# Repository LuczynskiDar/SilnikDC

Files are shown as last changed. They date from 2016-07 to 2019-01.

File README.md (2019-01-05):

# DC Engine driver ( Sterownik prędkości silnika DC )

> DC Engine driver is a [post graduate thesis](https://github.com/LuczynskiDar/SilnikDC/blob/master/Praca%20Podyplomowa%20-%20Sterownik%20Silnika%20-%20Dariusz%20%C5%81uczy%C5%84ski.pdf) done for AGH Univerisity of Science and Technology.

## Purpose of project

The purose of project was to use ECAD, EAGLE to design a circuit analog with
PCBA, then wirte a C program for Atmega32 to dirive a DC Enginge.

### Design approach

- For the project purposes will be used an mocro's internal clock,instead of using more reliable external crystal.
- Drivig the engine will be done on the basis of 4 switches, 2 for changing engine directions (Left/Right),
  which is actually changing micro's GPIO  and 2 responsible for incrementing and decrementing PWM signal.
- Interruption mechanism won't be used.
- I will use built in Fast PWM mechanism.
- The software will be done in C, usng Atmega Studio 7.
- The code will be debugged and uploaded thoreugh JTAG with MK7 Dragn programmer.
- Thce code will be validated with an eval board, Kamami ZL3.

### Block diagram

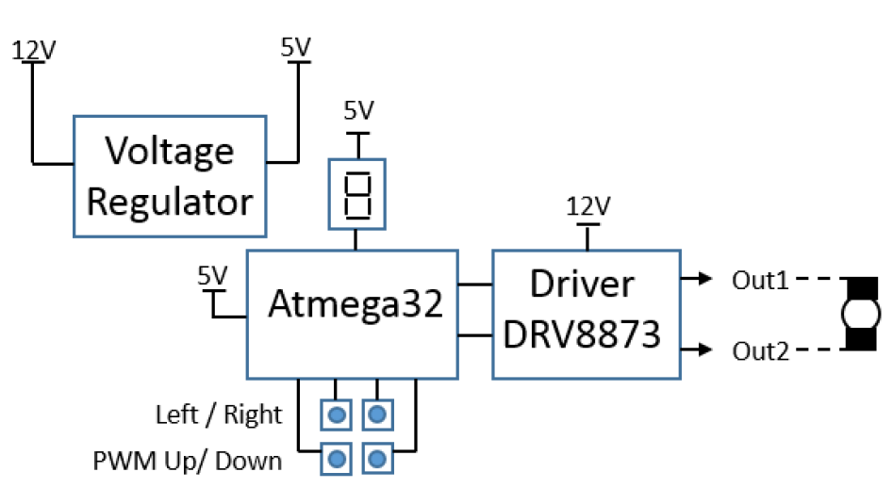
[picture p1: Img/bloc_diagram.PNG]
Block diagram


### Eagle ECAD designer

There are 2 Eagle project files:

- [Sterownik_DC.sch](https://github.com/LuczynskiDar/SilnikDC/blob/master/Sterownik_DC.sch) 
- [Sterownik_DC.brd](https://github.com/LuczynskiDar/SilnikDC/blob/master/Sterownik_DC.brd)

#### Schematic drawing

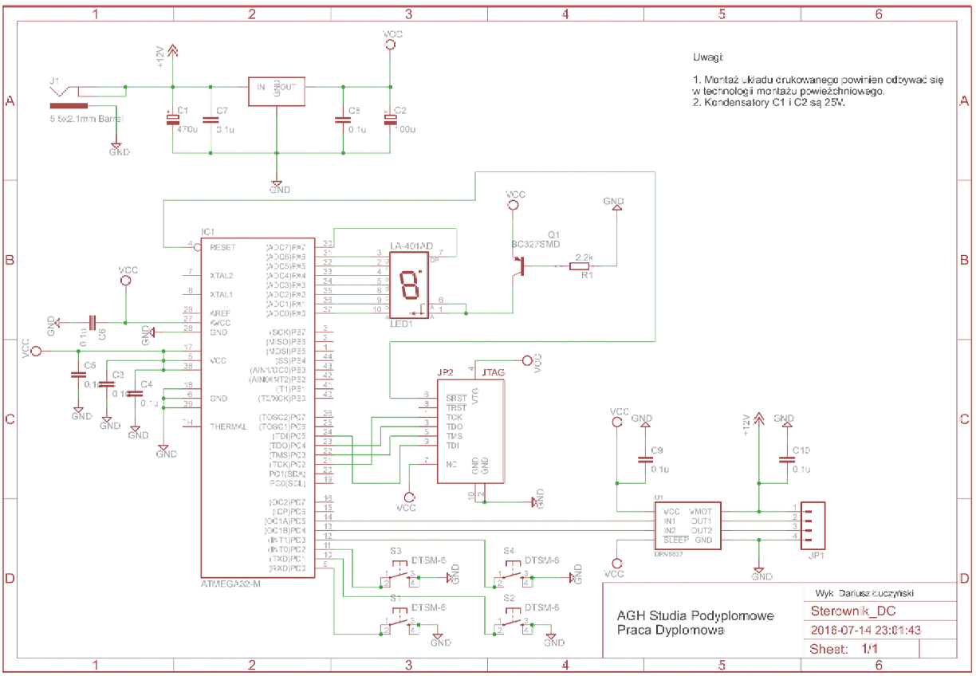
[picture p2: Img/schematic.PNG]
Schematics


#### Material List (BOM)

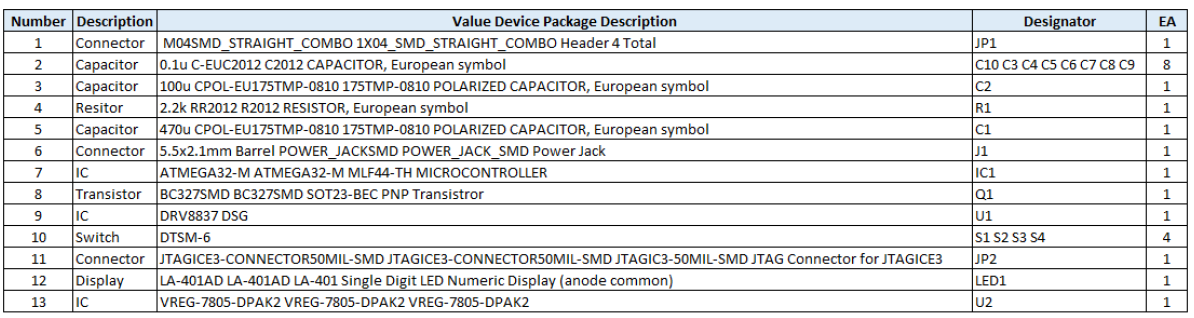
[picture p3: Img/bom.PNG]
BOM


#### Printed wiring board

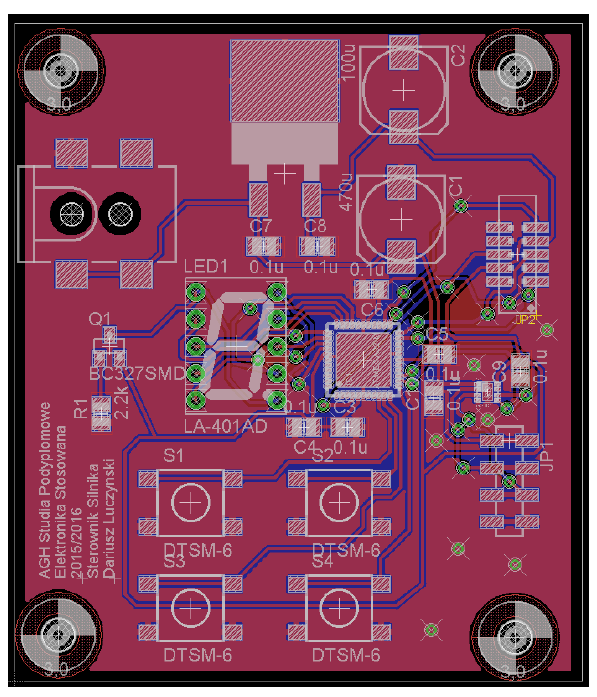
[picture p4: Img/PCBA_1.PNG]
PCBA view


#### PWB Drawing

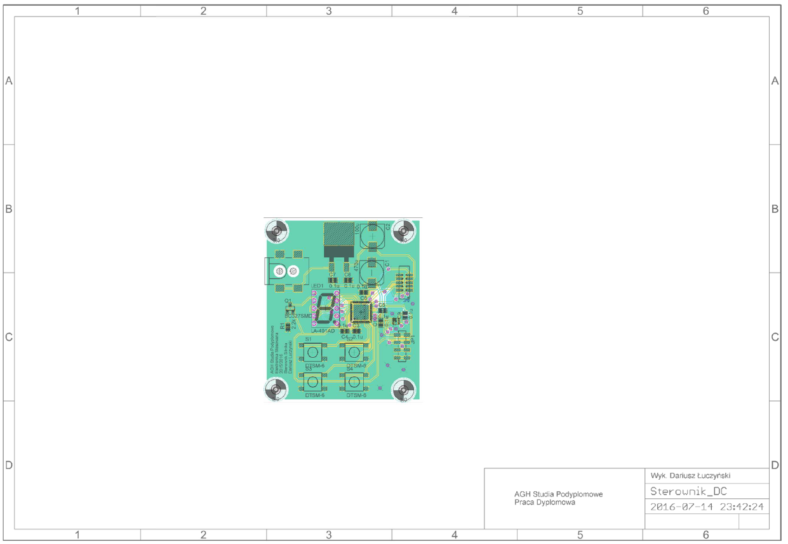
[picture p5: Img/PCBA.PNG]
PCBA drawing view


### C Code

I created 2 files,

- [constants.h](https://github.com/LuczynskiDar/SilnikDC/blob/master/Sterownik_DC/constants.h), which contains definition for an internal clock flags,
- [sterownikdc.c](https://github.com/LuczynskiDar/SilnikDC/blob/master/Sterownik_DC/sterownikdc.c), which contains other methods along with main loop ```while(1)```.

### Design Verification

Code verificationn was performed on eval board, all 4 swithches were working properly.

- Set the dc engine to turn left, "l" on the display.

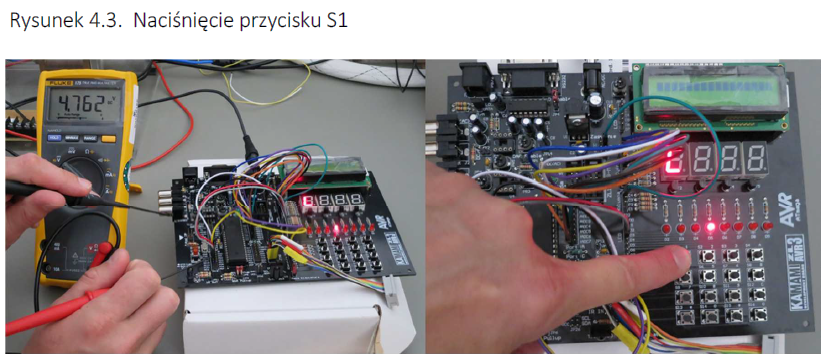
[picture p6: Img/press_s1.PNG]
Press S1


- Set the dc engine to turn right, "r" on te display.

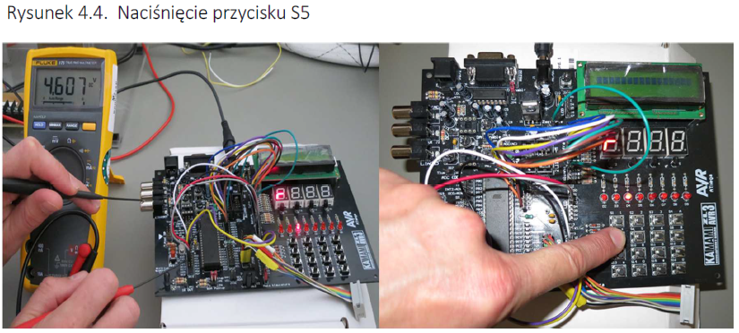
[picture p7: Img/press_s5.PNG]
Press S5


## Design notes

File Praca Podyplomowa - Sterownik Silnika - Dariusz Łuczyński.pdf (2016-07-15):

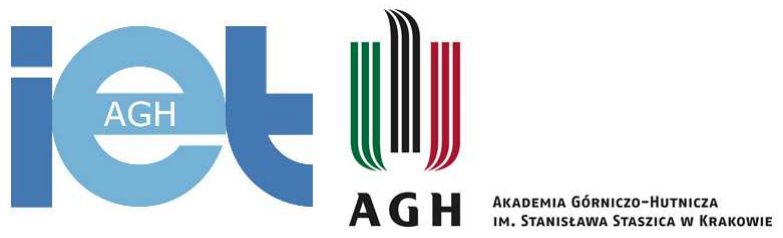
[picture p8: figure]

Studia podyplomowe – Elektronika Stosowana Wydział IEiT, rok akademicki 2015/2016

## Praca Podyplomowa

## Projekt sterownika prędkości silnika DC z wykorzystaniem funkcji PWM mikrokontrolera ATMEGA 32

## Dariusz Łuczyński

2

# Spis Treści

3

# Rozdział 1. Wstęp

Zadaniem poniższej pracy podyplomowej jest projekt urządzenia, które pośredniczy pomiędzy silnikiem prądu stałego a człowiekiem oraz pozwala na jego sterowanie poprzez przyciski. Założeniem przy budowie poniższego sterownika jest spełnianie dwóch funkcji:

- zmiana kierunku obrotów silnika CW/CCW (Clockwise / Counter clockwise);
- zmiana wypełnienia sygnału PWM;

Zmiana kierunku obrotów silnika polega na naprzemiennym załączaniu sygnału sterującego na Out1 i Out2 oraz masy, tj. gdy na Out1 jest sygnał PWM to na Out2 jest masa i na zmianę.

Rysunek 1.1. Schemat ideowy układu.

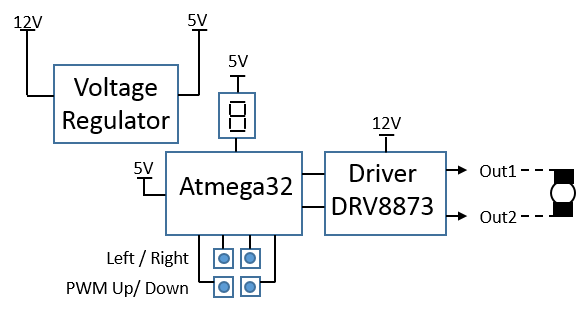
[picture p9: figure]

Rysunek 1.2. Modulacja PWM ( modulacja szerokości impulsu).

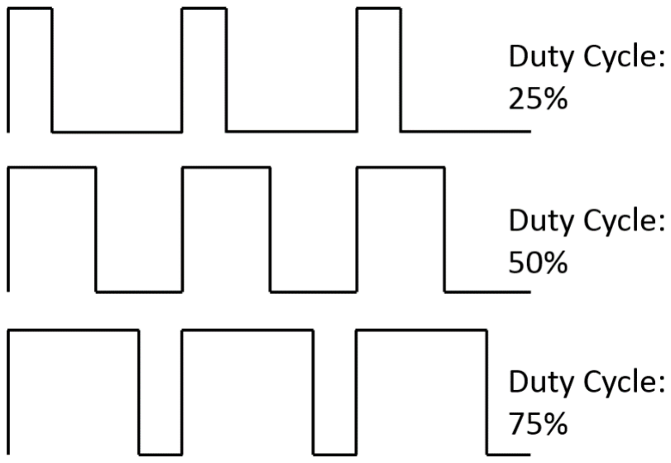
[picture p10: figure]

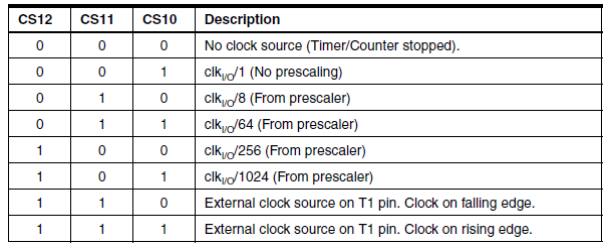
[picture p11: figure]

4

# Rozdział 2. Oprogramowanie mikrokontrolera

Podstawą procesora AVR jest czasomierz/licznik (Timer/Counter), w przypadku Atmega32 są to trzy timery, które zliczają impulsy zegarowe. Po osiągnięciu maksymalnej wartości licznik przekręca się i zaczyna zliczanie od nowa. Częstotliwość sygnału zegarowego określa minimalną rozdzielczość pomiaru, a każde zwiększenie licznika będzie następowało z tą rozdzielczością. Licznik po osiągnięciu wartości maksymalnej zaczyna zliczanie od początku. Atmega32 udostępnia dwa liczniki 8-bit oraz jeden 16-bit. Częstotliwość sygnału zegarowego może być podzielona, zmniejszona poprzez użycie Preskalera, poprzez użycie jednej z predefiniowanych wartości: 1, 8, 64, 256, 1024. Odbywa się to poprzez wybranie odpowiednich bitów Clock Select.

Rysunek 2.1. Preskaler Timera0 oraz Timera1.

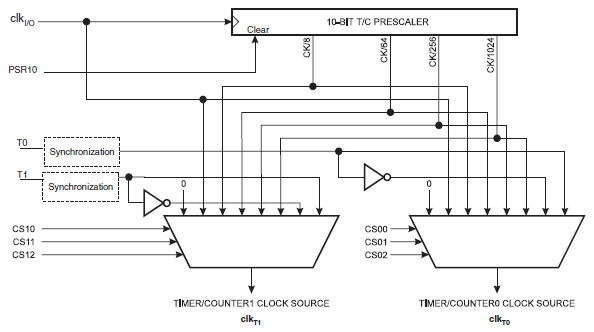
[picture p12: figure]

Tabela 2.1. Ustawienie bitów clock select.

5

Rysunek 2.2. Schemat blokowy Timera1.

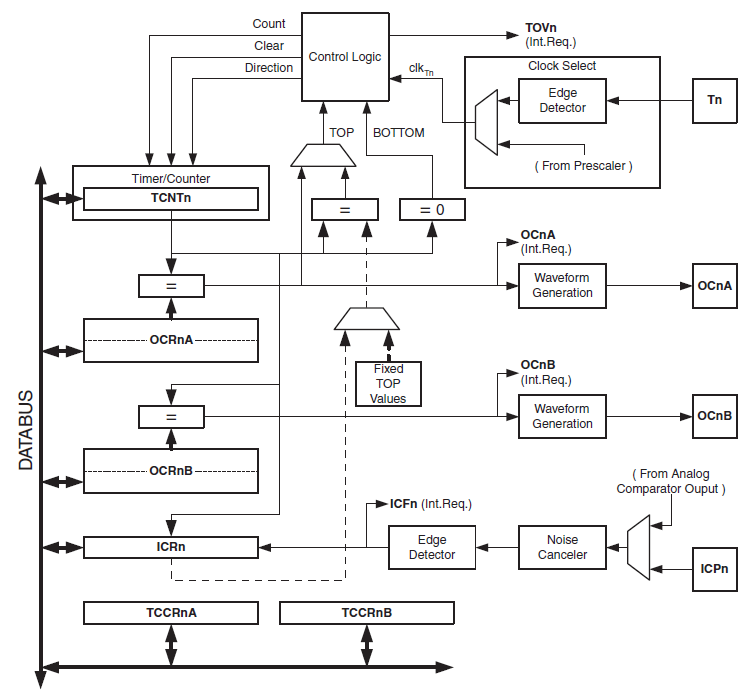
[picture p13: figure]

Początek może być wartością maksymalną, w przypadku liczników 8-bit jest 255, lub wartością minimalną, czyli 0. Mikrokontroler daje możliwość zliczania sygnałów od wartości minimalnej (Bottom) do maksymalnej (Top), oraz w przeciwnym kierunku. Zakładając, że kierunek zliczania impulsów jest w kierunku od Bottom do Top, to po osiągnięciu wartości 255 następuje zmiana flagi przepełnienia licznika TOV1 (Timer Overflow), co może skutkować wykonaniem procedury obsługi przerwania, o ile taka jest zdefiniowana w programie.

Tabela 2.2. Ustawienie bitów Waveform Generation Mode (WGM) dla Timera1

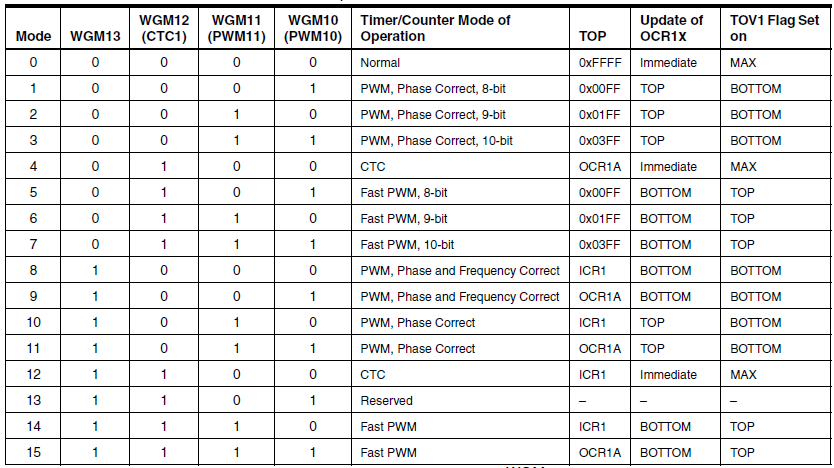
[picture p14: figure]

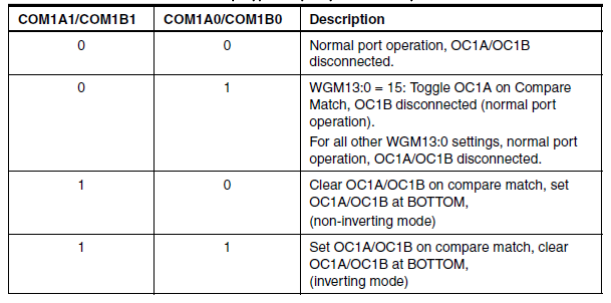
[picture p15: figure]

6

Zliczana wartość przez licznik, rejestr TCNT1, morze zostać porównana z wartością predefiniowaną przez użytkownika, wartością, która znajduje się w rejestrze OCR1A/OCR1B (Output Compare Register). Pozytywny wynik porównania rejestru licznika powoduje ustawienie flagi OCF1A/ OCF1B i skutkuje wystąpieniem zdarzenia Compare Match oraz może powodować wygenerowanie żądania wykonania obsługi przerwania. Compare Match może również służyć do wygenerowania przebiegów na pinach IO procesora, a jego wpływ na PINy jest określany poprzez odpowiednie ustawienie bitów COM0 i COM1.

Tabela 2.3. Znaczenie bitów COM w przypadku pracy timera w trybie FAST PWM

Rysunek 2.3. Tryb Fast PWM.

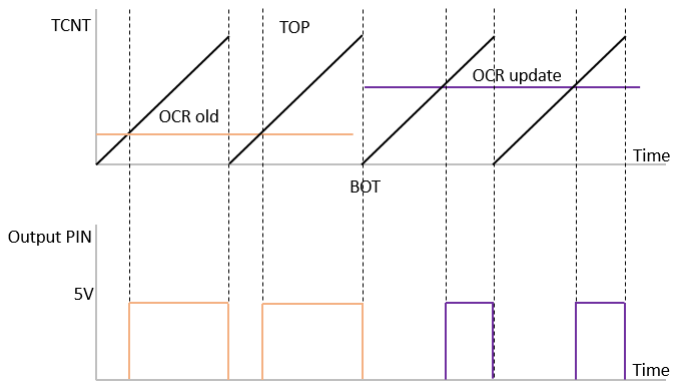
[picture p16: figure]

Stąd oprócz podstawowych funkcjonalności timera, to jest działania, jako licznik oraz precyzyjnego odmierzania czasu, mierzenia czasu między impulsami, dochodzi jeszcze

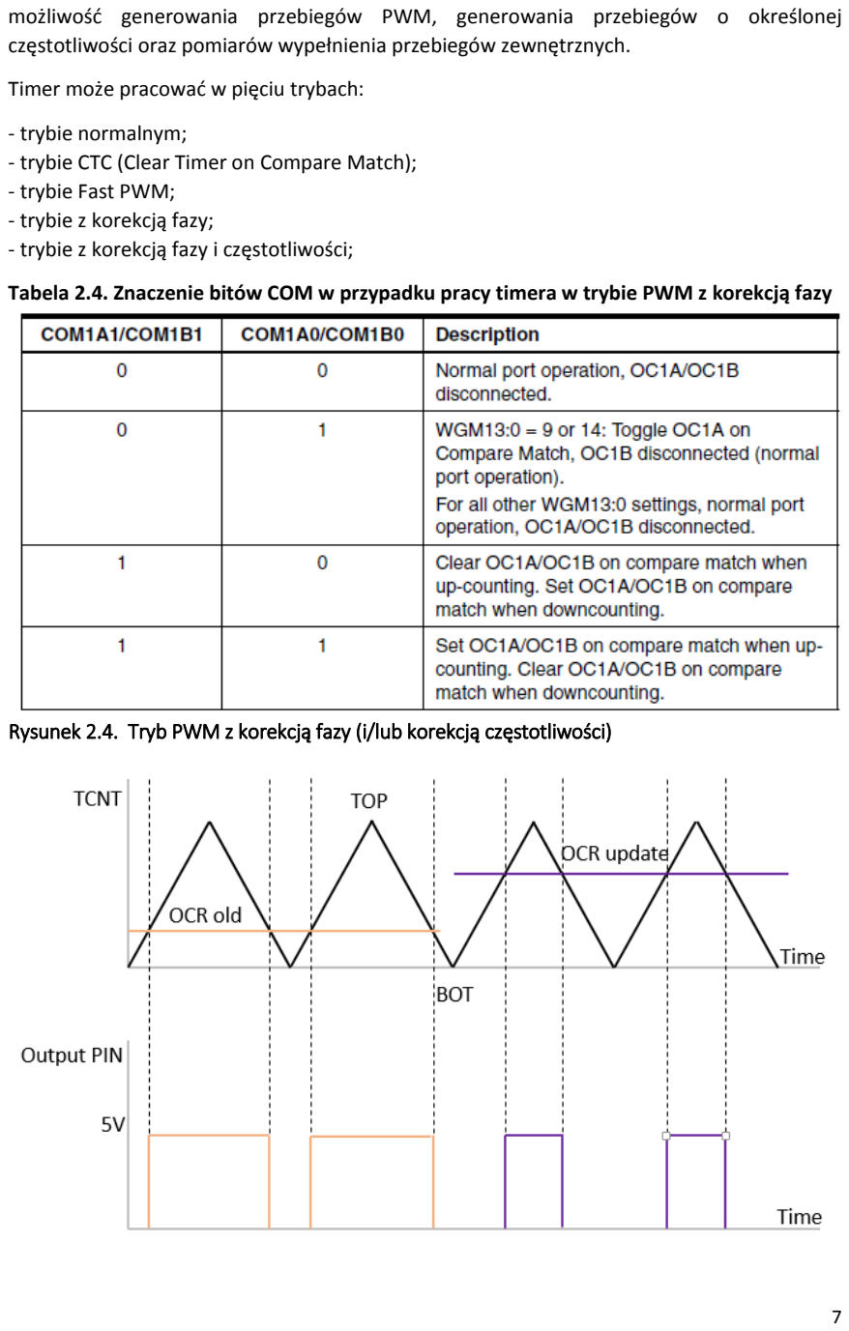
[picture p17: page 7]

7

możliwość generowania przebiegów PWM, generowania przebiegów o określonej częstotliwości oraz pomiarów wypełnienia przebiegów zewnętrznych.

Timer może pracować w pięciu trybach:

- trybie normalnym;
- trybie CTC (Clear Timer on Compare Match);
- trybie Fast PWM;
- trybie z korekcją fazy;
- trybie z korekcją fazy i częstotliwości;

Tabela 2.4. Znaczenie bitów COM w przypadku pracy timera w trybie PWM z korekcją fazy

Rysunek 2.4. Tryb PWM z korekcją fazy (i/lub korekcją częstotliwości)

8

W trybie normalnym, wbudowany Waveform Generation Mode nie jest wykorzystywany, natomiast używa się interwałów czasowych ograniczanych przez preskaler, w których na port wyjściowy, OC0 lub OC1, jest podawany stan wysoki.

Tryb CTC wymaga ustawienia odpowiednich bitów WGM, zgodnie z Tabelą 2.2, w rejestrach TCCR. Umożliwia na precyzyjniejszą kontrolę nad częstotliwością przebiegu na pinach wyjściowych, która wynosi Fclk / (2*Preskaler*(1+OCR1A)). Licznik zlicza do OCR1A, i za każdym razem, gdy osiąga tą wartość, generowane jest zdażenie TIMER1 COMP lub TIMER1 CAPT (o ile ustawiamy ICR). Przerwanie przepełnienia licznika TIMER1 OVF nie występuje, licznik nie zlicza do maksymalnej wartości.

Podobnie jak CTC tryb Fast PWM wymaga odpowiedniego zdefiniowania bitów WGM. Licznik zlicza od wartości Bottom do wartości Top, a po jej osiągnięciu, zlicza ponownie od wartości Bottom. Częstotliwość wynosi Fclk / (*Preskaler*(1+Licznik max)), gdzie Licznik max, jest maksymalną wartością trybu fast PWM, np. dla 8-bit jest to 255.

W przypadku trybów PWM z korekcją fazy oraz z korekcja fazy częstotliwości licznik odlicza od wartości Bottom do Top, a następnie od Top do Bottom, jak na Rysunku 2.4. Częstotliwość wynosi Fclk/(2*Preskaler(1+Wartość Top)). Oba tryby powinny mieć ustawione odpowiednie flagi WGM.

Przed przygotowaniem oprogramowania zostały przyjęte następujące założenia:

- zostanie wykorzystany wewnętrzny zegar mikroprocesora, bez posiłkowania się zewnętrznym rezonatorem kwarcowym;
- sterowanie będzie obywało się za pomocą czterech przycisków, a będzie realizować inkrementację i dekrementację sygnału PWM, a także zmianę wyjścia, na którym jest on podawany;
- do sterowania nie zostanie wykorzystany mechanizm przerwań;
- zostanie wykorzystany tryb Fast PWM;
- oprogramowanie zostanie napisane w języku C;

Oprogramowanie składa się z dwóch plików z kodem źródłowym, „constants.h” zawiera stałe oraz częstotliwość taktu zegarowego, natomiast w „sterownikdc.c” znajduje się pełen kod źródłowy programu.

Główny kod źródłowy programu definiuje globalne flagi, które określają, na jakim PIN jest PWM (OC1 lub OC0), oraz wartość wypełnienia. Jest zdefiniowana również tablica, która zawiera dwie zmienne ośmiobitowe typu unsign integer, służące do wyświetlania na przemian „l” lub „r”, w zależności od kierunku obrotów silnika. Tablica jest umieszczona w pamięci flash. W funkcji Main programu w pierwszej kolejności następuje inicjalizacja Timer1, za pomocą metody timer1_initialize(), ustawienie bitów WGM dla Fast PWM, bitów Compare Match A/B, a także rejestrów Output Compare Register A/B. Kierunek portów A zostaje ustawionyna wyjście, będą one obsługiwać wyświetlacz siedmiosegmentowy. Zostaje zdefiniowana częstotliwość Fclk/ (Preskaler * 256), w tym przypadku 1 MHZ/ ( 8 * 256), 488 Hz. Na czterech mniej znaczących bitach portu D zostaje ustawiony stan wysoki, porty te są wykorzystywane

9

do obsługi przycisków. Nieskończona pętla programu wywołuje kolejno trzy metody. Funkcja scan_key() sprawdza stan przycisków ( jest to tzw. pooling). Odczytywana jest wartość z rejestru PIND, natępenie zmieniana jest flaga lub wartość wypełnienia PWM. w zależności od tego, który przycisk został wciśnięty. Dekrementacja zmiennej counter, służy, jako mikroopóźnienie, ze względu na mechaniczne drgania przycisków występujące po ich naciśnięciu, „bouncing”. Funkcja show_direction() przełącza kierunek obrotów silnika oraz zmienia pokazywaną literę na wyświetlaczu siedmiosegmentowym. Ostatnia w kolejności metoda pwm_set() ma za zadanie ustawienie we właściwym OCR, wartości wypełnienia, która została uprzednio inkrementowana lub dekrementowana.

10

# Rozdział 3. Schemat elektryczny i obwód drukowany

Do układu zostaje doprowadzone 12V DC z zewnętrznego zasilacza impulsowego do 2.1 mm gniazda, które zostaje przekształcone na napięcie 5V, przy użyciu popularnej przetwornicy 7805.

Rysunek 3.1. Schemat stabilizatora napięcia.

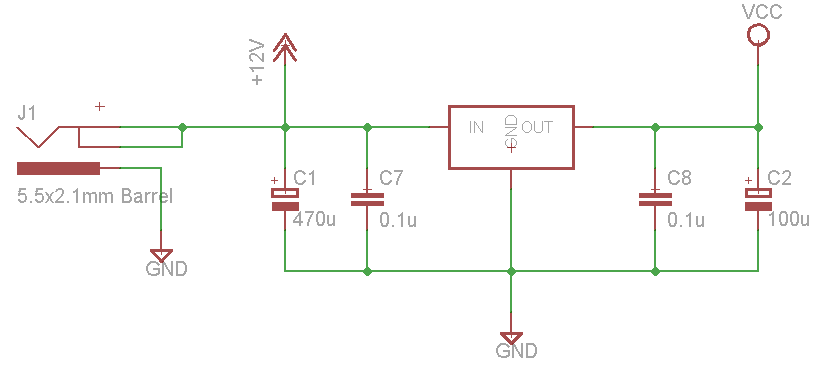
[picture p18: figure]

Z portu A zostało wyprowadzonych osiem bitów kontrolujących wyświetlacz siedmiosegmentowy, w tym DP. Zasilanie jest wpięte poprzez tranzystor BC327. Wyświetlacz jest typu: wspólna anoda. Musi zostać podany stan niski, aby świeciły poszczególne segmenty. Do portu C jest doprowadzony interfejs JTAG. Do portu D0~D3 zostały przyłączone linie odpowiadające za przyciski. Na liniach utrzymuje się stan wysoki, dopóki dany przycisk nie zostanie naciśnięty, zwarty do masy. Linie D4 (OC1B) i D5 (OC1A) doprowadzają sygnał PWM do drivera. W projekcie został użyty driver DRV8837 TI, niemniej nie jest to najlepszy wybór, ponieważ Vmot, 12V, w tym przypadku przekracza maksymalne napięcie z karty katalogowej.

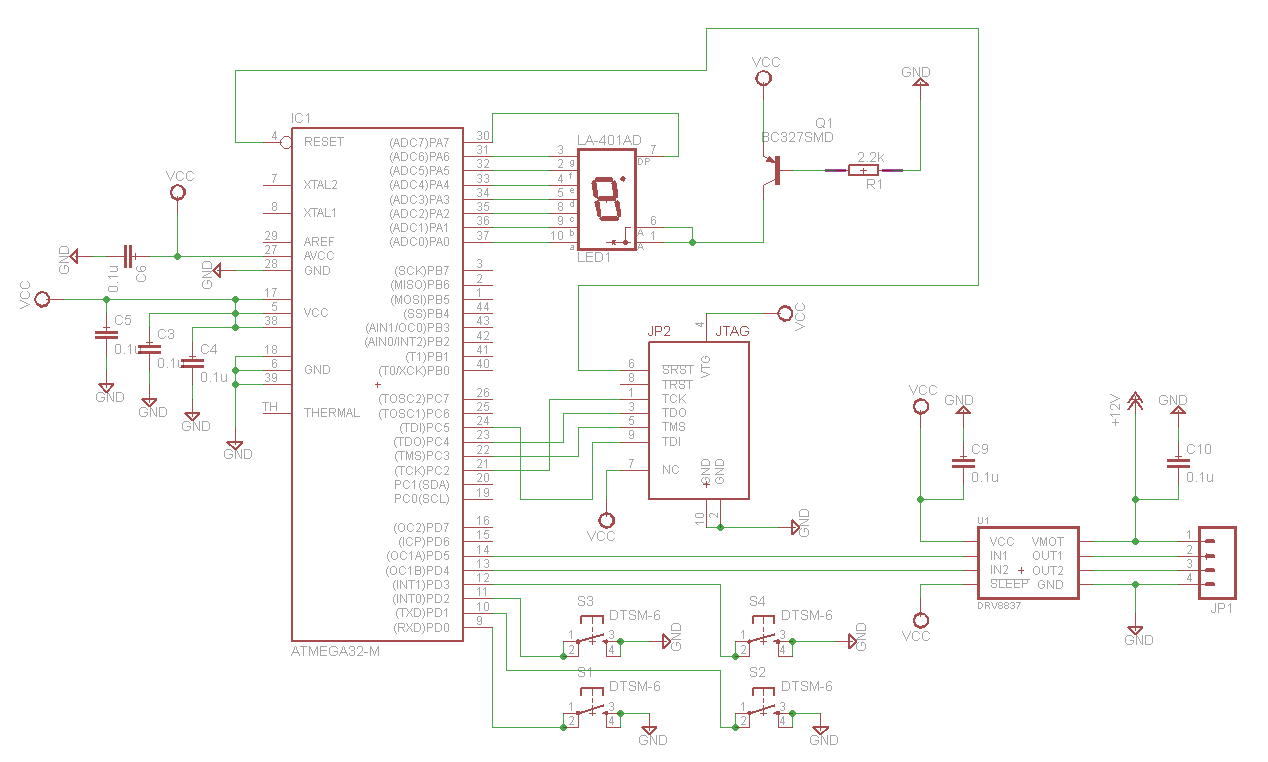
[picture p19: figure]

Rysunek 3.2. Schemat elektryczny układu sterującego.

11

Obwód drukowany został przygotowany przede wszystkim do montażu powierzchniowego, niemniej na płycie znajduje się jeden komponent z wyprowadzeniami przewlekanymi ( wyświetlacz LA-401AD). Wszystkie komponenty są montowane po stronie TOP, niemniej ścieżki zostały poprowadzone po stronie TOP jak i BOT. Ścieżki są 10 MILS, wynika to z ‘footprintu’ mikrokontrolera. Sygnały wyjściowe ze sterownika DRV8837 oraz masa i napięcie zasilające zostały wyprowadzone cztero-pinowym gniazdem wykonanym w technologii SMD.

Rysunek 3.3. Obwód drukowany.

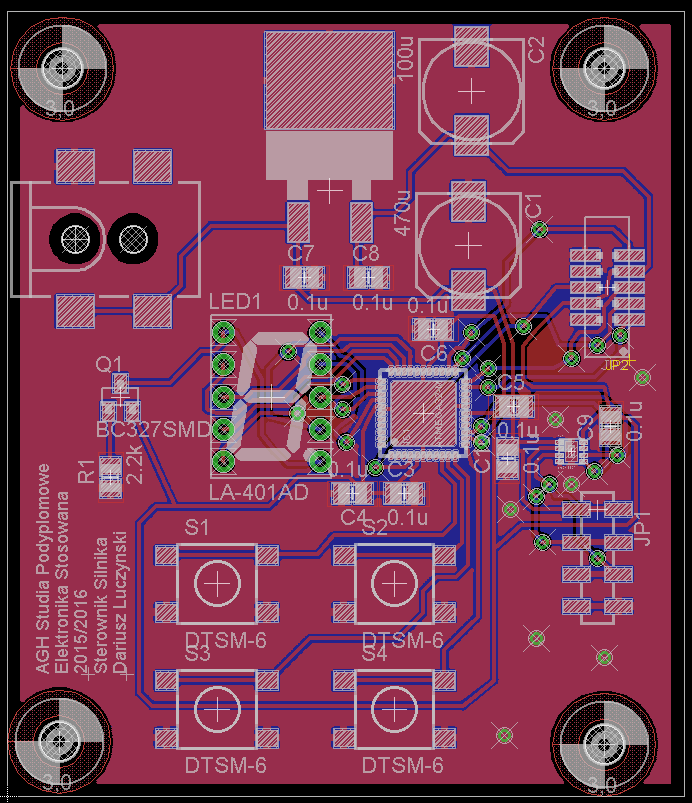
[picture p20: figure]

Pojedynczy obwód drukowany nie jest wystarczającym projektem, w przypadku produkcji większej niż prototypowa. Takie PCB należy „zpanelizować”, tj. połączyć w minimum cztery obwody na jednym laminacie, pozwoli to zredukować koszty produkcji. Należy również dodać tzw. „fiduciale”, czyli znaczniki, które pozwolą maszynom Pick’n’Place właściwie ustawić początek układów współrzędnych.

12

# Rozdział 4. Testy

Do sprawdzenia poprawności działania programu został użyty zestaw uruchomieniowy Kamami ZL3. Do JP24, wyprowadzenia wyświetlacza W1, zostały wpięte linie portu A (JP17). Pin pierwszy JP28 został podłączony do uziemienia. Do portów D0~D3 (JP19) został przyłączona „mała klawiatura”: S1, S5, S9, S13. Na JP3 została założona zwora. OC1B ( port D4) zostało podane na pin trzeci, natomiast OC1A na pin czwarty JP22.

Rysunek 4.1. Schemat elektryczny zestawu uruchomieniowego ZL3.

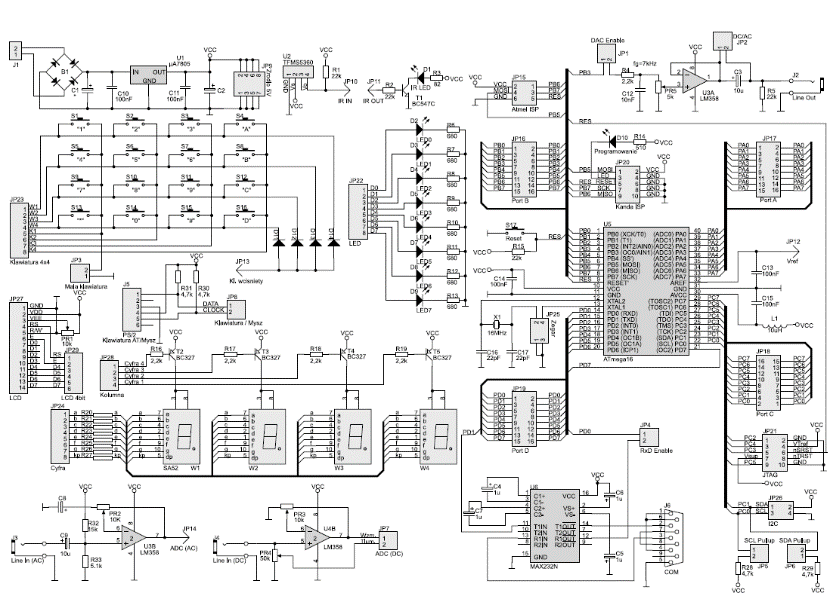
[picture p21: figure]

Rysunek 4.2. Podłączenie we/wy na ZL3.

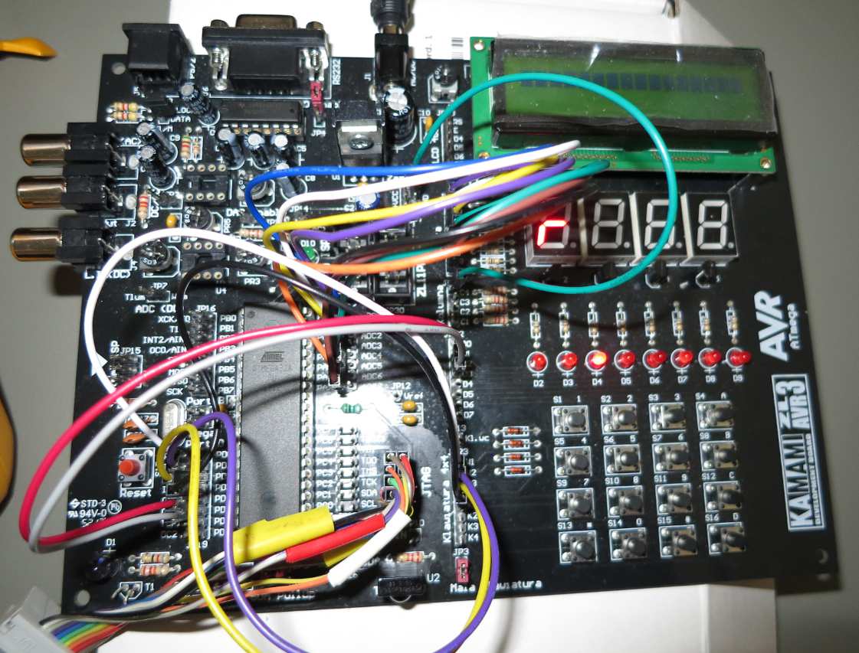
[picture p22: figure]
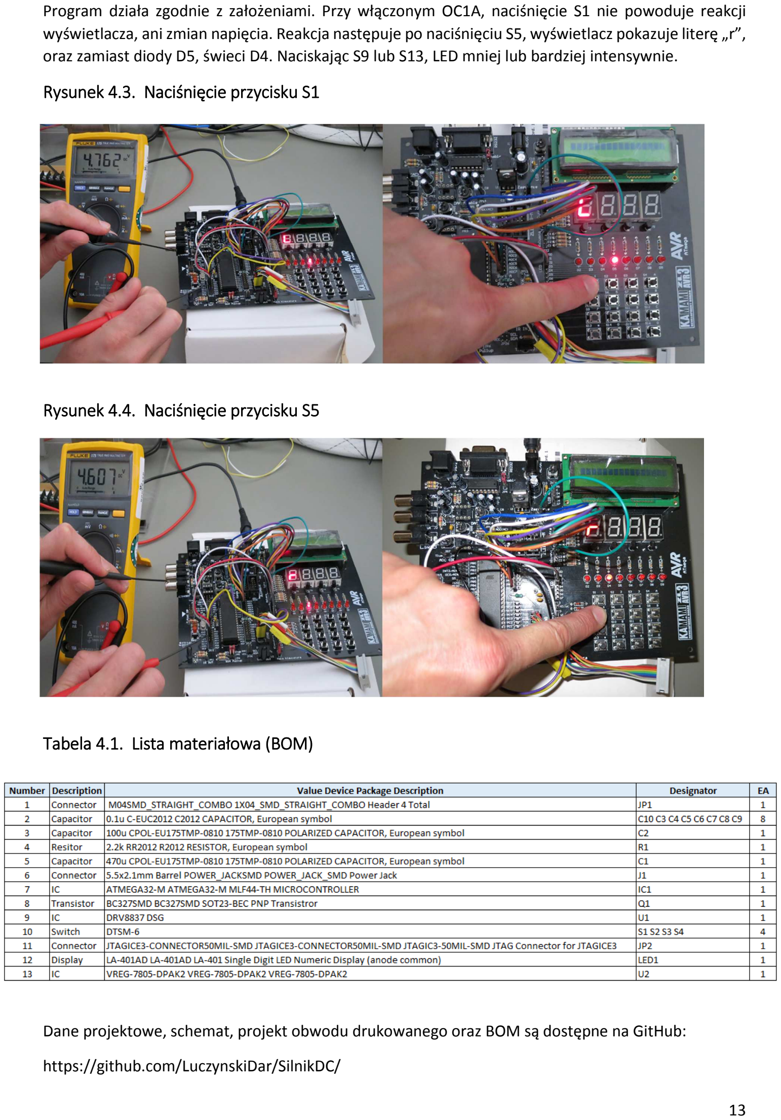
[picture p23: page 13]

13

Program działa zgodnie z założeniami. Przy włączonym OC1A, naciśnięcie S1 nie powoduje reakcji wyświetlacza, ani zmian napięcia. Reakcja następuje po naciśnięciu S5, wyświetlacz pokazuje literę „r”, oraz zamiast diody D5, świeci D4. Naciskając S9 lub S13, LED mniej lub bardziej intensywnie.

Rysunek 4.3. Naciśnięcie przycisku S1

Rysunek 4.4. Naciśnięcie przycisku S5

Tabela 4.1. Lista materiałowa (BOM)

Dane projektowe, schemat, projekt obwodu drukowanego oraz BOM są dostępne na GitHub:

https://github.com/LuczynskiDar/SilnikDC/

14

# Rozdział 5. Wykonanie projektu

Dalszym etapem jest wygenerowanie, bazując na zaprojektowanym obwodzie drukowanym, tzw. „gerberów”, czyli plików CAM (Computer Aided Manufacturing), NC Drill wskazujących miejsce oraz średnicę wierteł, oraz plików tekstowych zawierających koordynaty dla maszyn do montażu powierzchniowego. Gerbery do produkcji obwodu drukowanego należy przesłać do jednego z lokalnych producentów PCB: Hatron, Techno-Service, Evatronix etc. Pliki opisujące apertury dla matryc do sitodruku należy udostępnić firmie produkującej tzw. „stencile”, np. Scanditron lub Semicon. Do montażu powierzchniowego można użyć pasty lutowniczej ołowiowej (OM-5100) lub bezołowiowej (np. nisko srebrowa OL107F). Wyświetlacz siedmiosegmentowy, jedyny element przewlekany, można przylutować ręcznie, lub przy użyciu niewielkiego tygla lutowniczego.

Rysunek 5.1. HAKKO FX-300, Dip solder system /hakko.com/

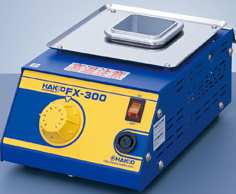
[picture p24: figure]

Należy pamiętać, że skala produkcji powinna być uzasadniona zwrotem z inwestycji.

15

# Bibliografia

### 1. ATmega32 (32L) - 8-bit AVR Microcontroller with 32KBytes In-System Programmable

Flash.

### 2. Język C dla mikrokontrolerów AVR. Od podstaw do zaawansowanych aplikacji, Tomasz

Francuz, Helion 2011.
3. AVR Atmega w praktyce. Rafał Baranowski, BTC 2015.

16

# Załącznik A. Kod programu

Kod programu A.1. Constants.h

#ifndef CONSTANTS_H_

#define CONSTANTS_H_

//Clock
#define F_CPU 1000000UL

// Display LEDs
#define KEYS 2

// Definition of default PWM, which is 40% duty cycle #define PWMDEF 102
#define PWMGND 0

#endif /* CONSTANTS_H_ */

Kod programu A.2. Sterownikdc.c

/*
* Sterownik_DC.c
*
* Author : Dariusz Luczynski */

#include "constants.h"

#include <avr/pgmspace.h>

#include <stdlib.h>

#include <util/delay.h>

#include <avr/io.h>

#include <avr/interrupt.h>

//To set the two element LED display
static const uint8_t PROGMEM DIRECTION[2]={0xC7, 0xAF};

// The direction indicator flag
static uint8_t dir_flag = 0xFF;

static uint8_t handler = 0;
// Direction flag indicator volatile uint8_t pwm_flag=0xFF;

volatile uint8_t pwm_handler=102;

// Read pins indicator
volatile uint8_t pin_reader;

// Initialization of Timer1 for the PWM outputs
void timer1_initialize(void)
{

// To set the prescaler to divide the frequency per 8, resulting 488 Hz TCCR1B |= (1<<CS11);
// To set the Waveform Generator Mode to 8-bit Fast PWM

17

TCCR1A |= (1<<WGM10);
TCCR1B |= (1<<WGM12);
// Set the PINs to zero, after the compare match event, // when the minimum value is being reached
TCCR1A |= (1<<COM1A1) | (1<<COM1B1) ;

// Set to the direction registers, PIN 4 and PIN5
DDRD |= (1<<PD4) | (1<<PD5);

//Initialize output compare registers
OCR1A = | PWMDEF;
OCR1B = PWMGND;

}

//To chose from the tables a proper value for a proper LED display //Inline do not recall the function just puts the code of the function there

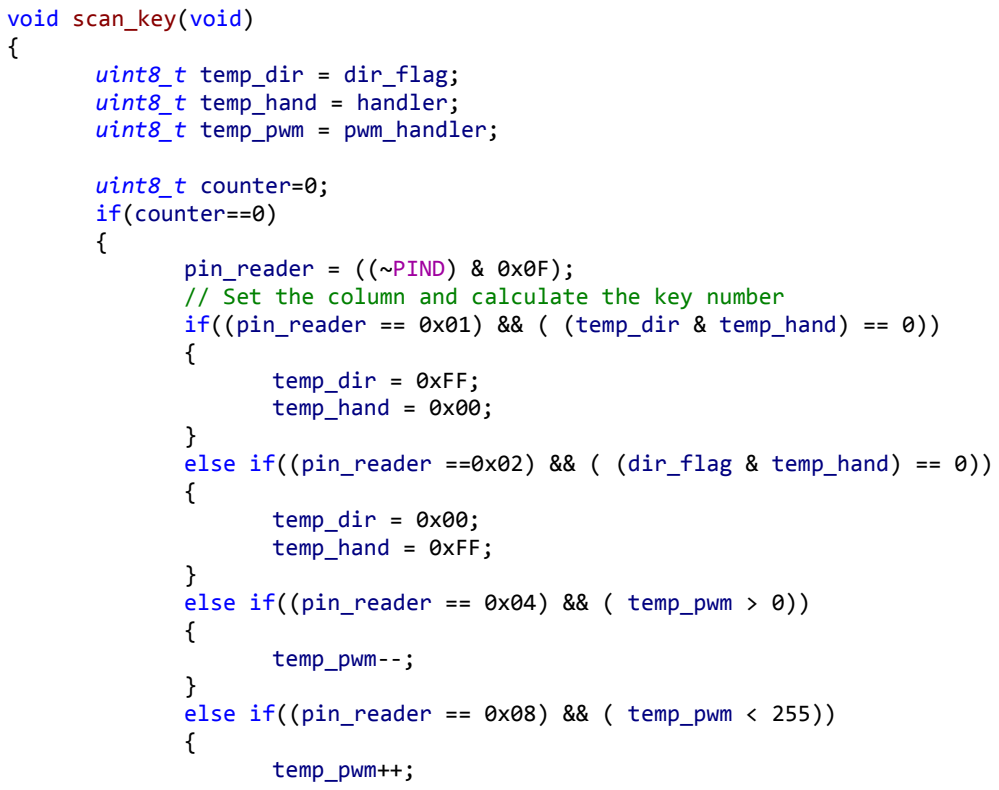
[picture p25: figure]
void scan_key(void) {; uint8_t temp_dir = dir_flag; uint8_t temp_hand = handler; uint8_t temp_pwm = pwm_handler;; uint8_t counter=0; if(counter==0) {; pin_reader = ((~PIND) & 0x0F);; temp_dir = 0xFF; temp_hand = 0x00;; temp_dir = 0x00; temp_hand = 0xFF;; temp_pwm--;; temp_pwm++;

// Set the column and calculate the key number if((pin_reader == 0x01) && ( (temp_dir & temp_hand) == 0))

else if((pin_reader ==0x02) && ( (dir_flag & temp_hand) == 0))

else if((pin_reader == 0x04) && ( temp_pwm > 0))

else if((pin_reader == 0x08) && ( temp_pwm < 255))

}
counter=100;
} else counter--;

dir_flag = temp_dir;
handler = temp_hand;
pwm_handler = temp_pwm;
}

void pwm_set(void)
{
if (pwm_flag == 0xff) OCR1A = pwm_handler; if (pwm_flag == 0x00) OCR1B = pwm_handler; }

18

void show_direction( void)

{
uint8_t temp = 0xFF;
uint8_t pwm_holder;
PORTA = 0xFF;
if(dir_flag == 0xFF)
{
temp = pgm_read_byte(&DIRECTION[0]);

pwm_holder = OCR1A;
DDRD &= ~(1<<PD4);
DDRD = (1<<PD5);
OCR1B = pwm_holder;
pwm_flag = 0xFF;
}
if(dir_flag == 0x00)
{
temp = pgm_read_byte(&DIRECTION[1]); pwm_holder = OCR1B;
DDRD &= ~(1<<PD5);
DDRD = (1<<PD4);
OCR1A = pwm_holder;
pwm_flag = 0x00;
}
PORTA = temp;
}

int main(void)
{
timer1_initialize();
DDRA = 0xFF;
PORTD |= 0x0F;
while (1)

{
scan_key();
show_direction();
pwm_set();
_delay_ms(10);
}
}

19

Załącznik B. Schemat elektryczny układu.

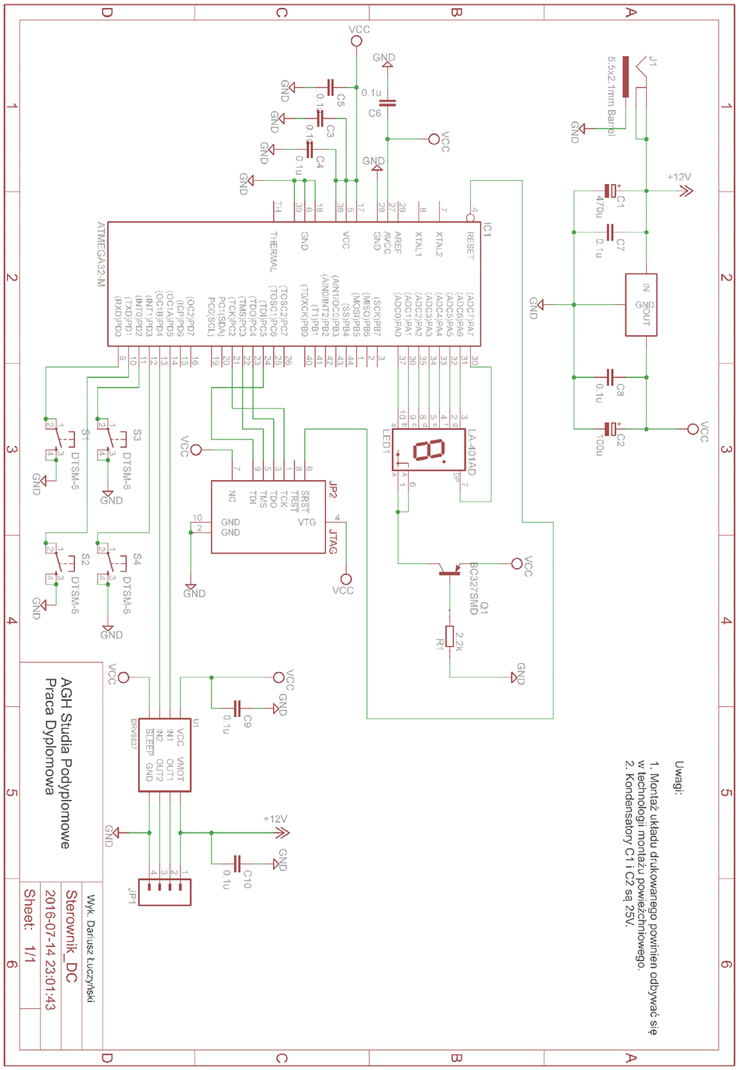
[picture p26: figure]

20

Załącznik C. Obwód drukowany.

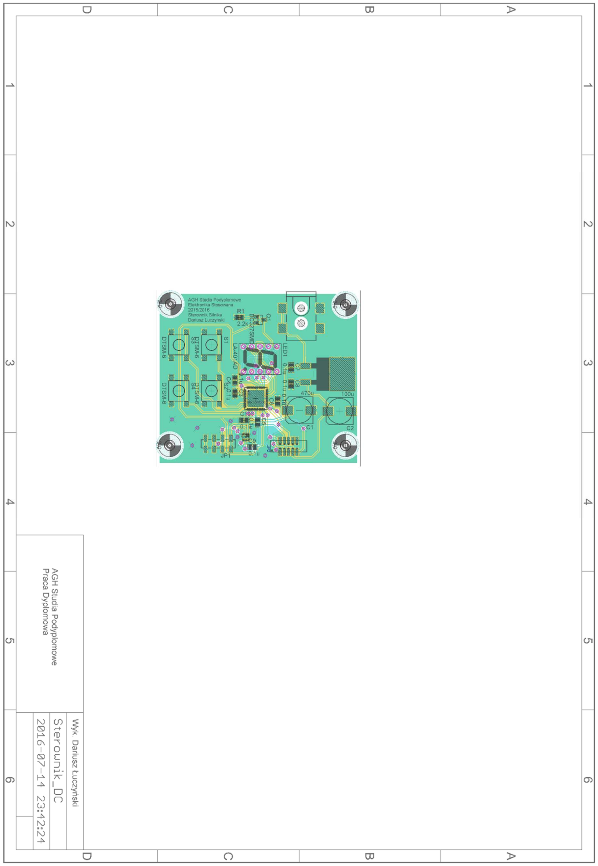
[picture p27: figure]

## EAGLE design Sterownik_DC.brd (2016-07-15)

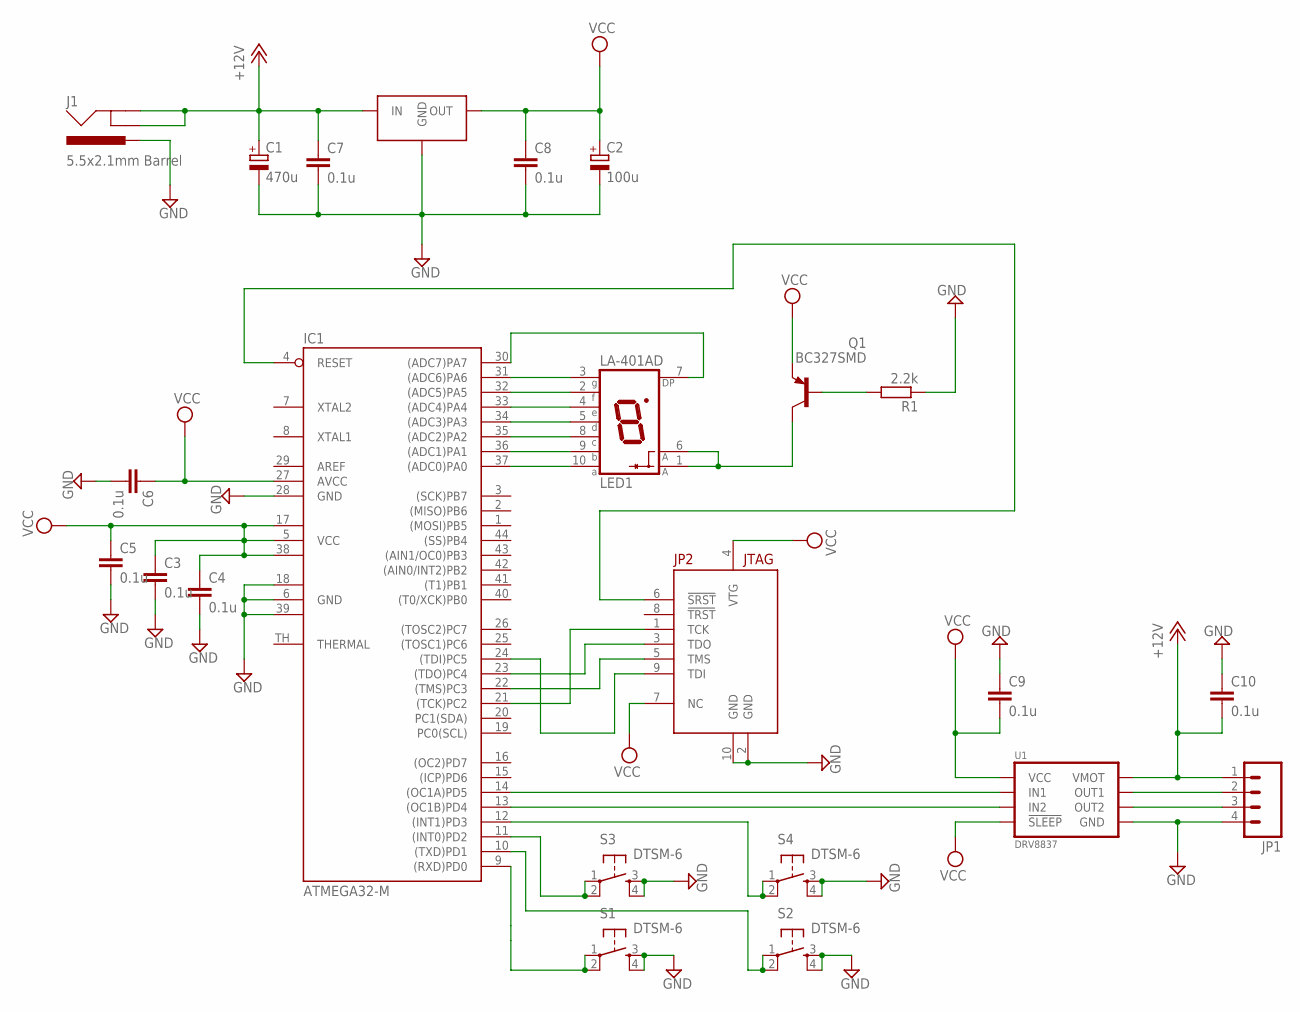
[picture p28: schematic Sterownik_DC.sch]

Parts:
C1: 470u; 175TMP-0810
C2: 100u; 175TMP-0810
C3, C4, C5, C6, C7, C8, C9, C10: 0.1u; C2012
IC1: ATMEGA32-M; MLF44-TH
J1: 5.5x2.1mm Barrel; POWER_JACK_SMD
JP1: M04SMD_STRAIGHT_COMBO; 1X04_SMD_STRAIGHT_COMBO
JP2: JTAGICE3-CONNECTOR50MIL-SMD; JTAGIC3-50MIL-SMD
LED1: LA-401AD; LA-401
Q1: BC327SMD; SOT23-BEC
R1: 2.2k; R2012
S1, S2, S3, S4: DTSM-6
U1: DRV8837; DSG
U$1: VREG-7805-DPAK2

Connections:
+12V: C1.+, C7.1, C10.2, J1.GND (GNDBREAK), J1.P$4 (GND), JP1.1, U1.1 (VMOT), U$1.VIN (IN)
GND: C1.-, C2.-, C3.2, C4.2, C5.2, C6.2, C7.2, C8.2, C9.1, C10.1, IC1.6 (GND), IC1.18 (GND1), IC1.28 (GND), IC1.39 (GND2), J1.VIN0 (PWR), JP1.4, JP2.2 (GND), JP2.10 (GND), R1.1, S1.3, S1.4, S2.3, S2.4, S3.3, S3.4, S4.3, S4.4, U1.4 (GND), U1.PAD (GND), U$1.GND
unnamed: JP1.2, U1.2 (OUT1)
unnamed: IC1.4 (RESET), JP2.6 (!SRST)
unnamed: IC1.35 ((ADC2)PA2), LED1.8 (C)
unnamed: Q1.B, R1.2
unnamed: IC1.11 ((INT0)PD2), S3.1, S3.2
unnamed: IC1.21 ((TCK)PC2), JP2.1 (TCK)
unnamed: IC1.23 ((TDO)PC4), JP2.3 (TDO)
unnamed: IC1.31 ((ADC6)PA6), LED1.3 (G)
unnamed: IC1.32 ((ADC5)PA5), LED1.2 (F)
unnamed: IC1.33 ((ADC4)PA4), LED1.4 (E)
unnamed: IC1.34 ((ADC3)PA3), LED1.5 (D)
unnamed: IC1.37 ((ADC0)PA0), LED1.10 (A)
unnamed: IC1.36 ((ADC1)PA1), LED1.9 (B)
unnamed: IC1.30 ((ADC7)PA7), LED1.7 (DP)
unnamed: LED1.1 (A), LED1.6 (A), Q1.C
unnamed: IC1.10 ((TXD)PD1), S2.1, S2.2
unnamed: IC1.22 ((TMS)PC3), JP2.5 (TMS)
unnamed: IC1.13 ((OC1B)PD4), U1.5 (IN2)
unnamed: IC1.12 ((INT1)PD3), S4.1, S4.2
unnamed: IC1.14 ((OC1A)PD5), U1.6 (IN1)
unnamed: IC1.9 ((RXD)PD0), S1.1, S1.2
unnamed: JP1.3, U1.3 (OUT2)
unnamed: IC1.24 ((TDI)PC5), JP2.9 (TDI)
VCC: C2.+, C3.1, C4.1, C5.1, C6.1, C8.1, C9.2, IC1.5 (VCC), IC1.17 (VCC1), IC1.27 (AVCC), IC1.38 (VCC2), JP2.4 (VTG), JP2.7 (NC), Q1.E, U1.7 (!SLEEP), U1.8 (VCC), U$1.VOUT (OUT)

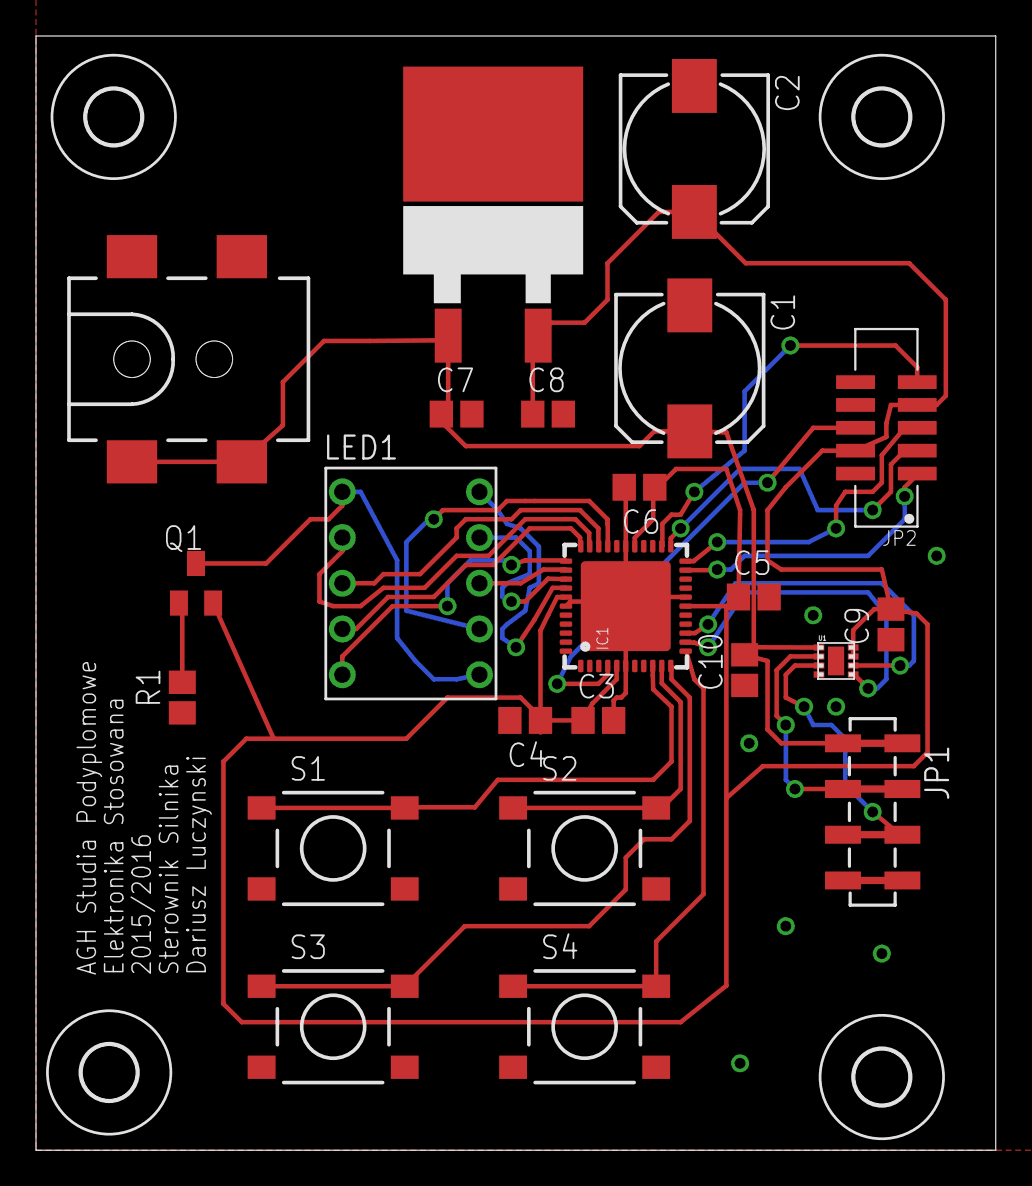
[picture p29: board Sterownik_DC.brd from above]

Board: 2 copper layers, 53.3 x 61.9 mm, 28 parts (0 on the bottom side), 26 nets.

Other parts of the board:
U$2, U$3, U$4, U$5: 3,0
U$6: A4L-LOC

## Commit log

2016-07-15 Add files via upload
    First commit
    [Sterownik_DC.brd, Sterownik_DC.sch]
2019-01-05 bom image

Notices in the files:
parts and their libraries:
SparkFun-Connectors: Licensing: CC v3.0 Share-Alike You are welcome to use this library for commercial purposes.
